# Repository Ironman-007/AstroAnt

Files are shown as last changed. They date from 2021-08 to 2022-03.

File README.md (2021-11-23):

# AstroAnt
Phase II of Rovables

The AstroAnt is the second generation of the Rovable project. The AstroAant also use magnetic wheels to attach to magnetic surface.

The AstroAnt is a modular design, and can carry different sensors to finish different kinds of diognostic missions, such as finding abnormal heating source, check CO2 leakage, detect metal flaw, and streaming video from remote.

Files descriptions:

- The 3D model of the robot is in the [Small_magnets_R821_with_gearbox](3dmodel/Small_magnets_R821_with_gearbox).

- The firmware of the robot is in [AstroAnt](Software/AstroAnt).

- The PC program (UI) is the [gui.py](Software/GUI_python/gui.py). Open with command line: ```python3 gui.py```

- The PCB design is in the [PCB](PCB). The [mainboard_v1](PCB/Mainboard/mainboard_v1/) is the design of the main control board, developed with KiCAD. The others are sensor modules design.

- The software of the central station for collecting data and distributing command is in [central_station](Software/Central_station/central_station/).

- The software of the central station for Camera in [cam_central](Software/Central_station/cam_central/).

- The Box design for the Zero-G flight test is in [Ant_Test_Box_DEC](3dmodel/Ant_Box_DEC/).

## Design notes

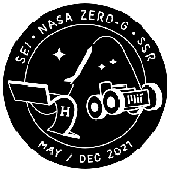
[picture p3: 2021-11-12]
PCB/Control_pad/patch-design-options3[3797].png

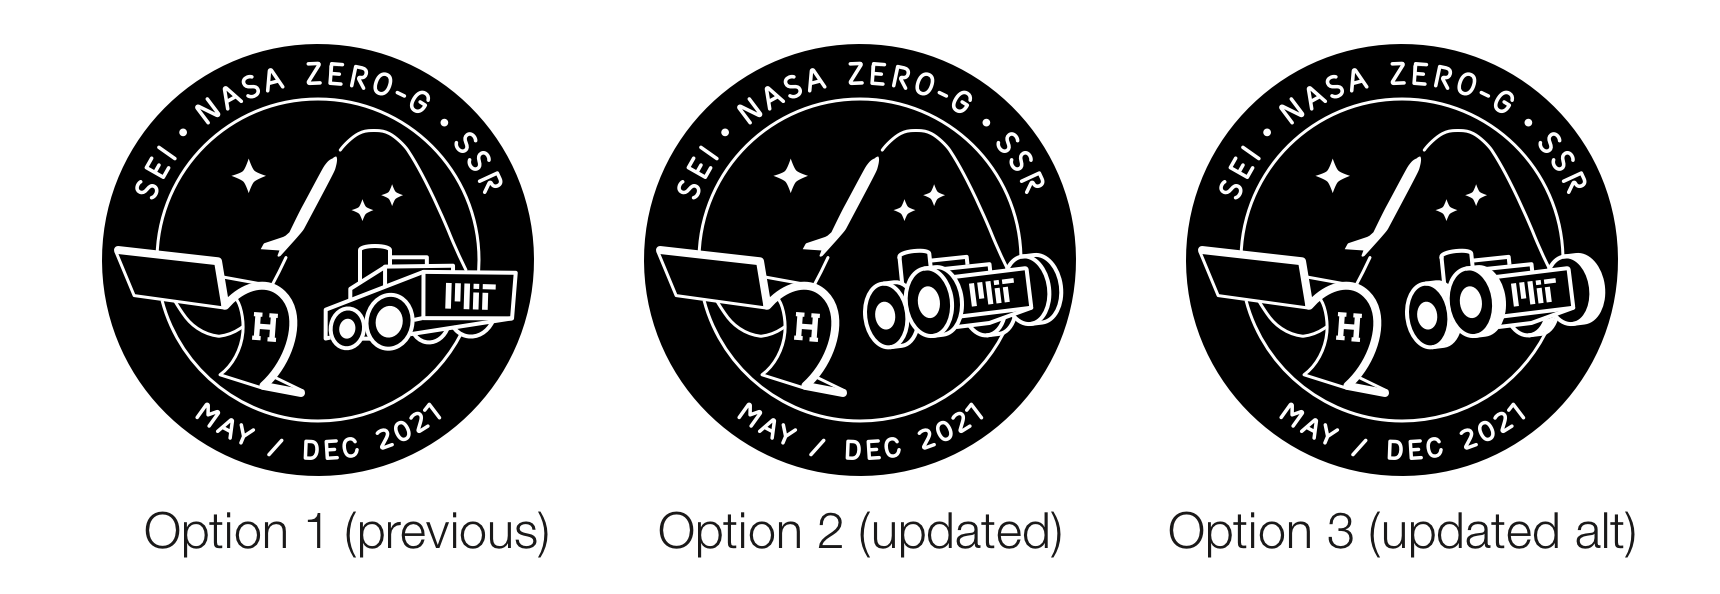
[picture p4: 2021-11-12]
PCB/Control_pad/patch-design-options3[3797] - Copy.png

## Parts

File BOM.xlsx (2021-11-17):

220mAh LiPo Battery | https://www.amazon.com/220mAh-Battery-Charger-Eachine-Quadcopter/dp/B07J3XJRF8
2x5x2.5mm ball bearing | https://www.amazon.com/2x5x2-5mm-MR52-ZZ-Precision-Bearings-Chrome/dp/B00TVPSCVO
Magnets | https://www.kjmagnetics.com/proddetail.asp?prod=RA22CS-N-N52
Ball bearing | https://www.amazon.com/uxcell-MR84-2RS-Bearing-4x8x3mm-Bearings/dp/B07TRQ19Y5
Name | Link | Qty | Vender
6mm pogo ping | https://www.amazon.com/Mxfans-Gold-plated-Copper-Needles-Connector/dp/B07FQF2BRC | 1 | amazon
9mm pogo ping | https://www.amazon.com/Mxfans-Gold-Plated-Copper-Needles-Thimble/dp/B07FQ52W88 | 1
SCD41 | https://www.digikey.com/en/products/detail/sensirion-ag/SCD41-D-R2/13684005 | 5 | digikey
SCD40 | https://www.digikey.com/en/products/detail/sensirion-ag/SCD40-D-R2/13684003 | 5
TPIS 1S 1385 / 5029 | https://www.digikey.com/en/products/detail/excelitas-technologies/TPIS-1S-1385-5029/9760638 | 10
RJD3555HPPV30M | https://www.digikey.com/en/products/detail/illinois-capacitor/RJD3555HPPV30M/6159145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 | 10
RFM97CW | https://www.sparkfun.com/products/18084 | 10 | Sparkfun
RFM95CW | https://www.sparkfun.com/products/18085 | 10
Aluminum frame | https://www.mcmaster.com/47065T101-47065T121/ | 10 | MacMaster Carr
Aluminum frame | https://www.mcmaster.com/47065T101-47065T209/ | 5
Handles | https://www.mcmaster.com/5190A3/ | 4
Screws | https://www.mcmaster.com/90991A122/ | 1
Screws | https://www.mcmaster.com/92832A334/ | 2
Screws | https://www.mcmaster.com/90991A123/ | 1
T-Slotted Framing | https://www.mcmaster.com/3136N153/ | 3
Flament (PETG) | https://www.matterhackers.com/store/l/pro-series-petg/sk/M89FGW3P | 2 | Matter hacker
Solder | https://www.amazon.com/dp/B0759P8GBZ | 1
Name | Link | Qty | Vender
nRF52840 module | https://www.amazon.com/Raytac-MDBT50Q-U1MV2-Bluetooth-Connector-Pre-Certified/dp/B0851WK785 | 1 | amazon
LoRa antenna | https://www.digikey.com/en/products/detail/linx-technologies-inc/ANT-916-USP/3830737 | 40 | digikey
RJD3555HPPV30M | https://www.digikey.com/en/products/detail/illinois-capacitor/RJD3555HPPV30M/6159145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 | 5
heat insert | https://www.amazon.com/Keadic-M3x6mmx5mm-Threaded-Embedment-Printing/dp/B08ZS6F5QW | 3 | amazon
heat insert | https://www.amazon.com/Keadic-M3x6mmx5mm-Threaded-Embedment-Printing/dp/B08ZRY23NH | 2
heat insert | https://www.amazon.com/Keadic-M3x6mmx5mm-Threaded-Embedment-Printing/dp/B08ZS4L8G7 | 2
Sensor | https://www.adafruit.com/product/3660 | 5 | adafruit
Weller solder tips | https://www.amazon.com/ShineNow-Quality-Replacement-WELLER-WE1010NA/dp/B071KYGZT8 | 1

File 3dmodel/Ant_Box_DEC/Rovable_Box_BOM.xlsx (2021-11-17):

ITEM NO. | PART NUMBER | Link | QTY. | unit price
1 | 47065T209_ALUMINUM T-SLOTTED FRAMING EXTRUSION | https://www.mcmaster.com/47065T101-47065T209/ | 20 | 7.79 | 155.8
2 | 47065T267_ALUMINUM T-SLOTTED FRAMING EXTRUSION | https://www.mcmaster.com/47065T267/ | 16 | 7.62 | 121.92
3 | 47065T278_ALUMINUM T-SLOTTED FRAMING EXTRUSION | https://www.mcmaster.com/47065T278/ | 6 | 7.95 | 47.7
4 | 8982K5_4ft | https://www.mcmaster.com/8982K54-8982K541/ | 1 | 2.73 | 2.73
5 | 8982K5_2ft | https://www.mcmaster.com/8982K54-8982K546/ | 2 | 1.65 | 3.3
6 | 47065T239 | https://www.mcmaster.com/47065T239/ | 8 | 5.25 | 42
8 | 47065T236 | https://www.mcmaster.com/47065T236/ | 17 | 5.21 | 88.57
9 | 47065T736_T-SLOTTED FRAMING | https://www.mcmaster.com/47065T736/ | 8 | 9.99 | 79.92
10 | 92198A628 | https://www.mcmaster.com/92198A628/ | 1 | 3.47 | 3.47
11 | 1/4_20_nut | https://www.mcmaster.com/94600A500/ | 1 | 13.38 | 13.38
12 | Framing fastener | https://www.mcmaster.com/3136N279/ | 15 | 4.73 | 70.95
13 | 1/4_20_5/8_screw_flat | https://www.mcmaster.com/97654A353/ | 8 | 6.35 | 50.8
14 | 1/4_20_1/2_screw_flat | https://www.mcmaster.com/97654A262/ | 5 | 4.8 | 24
15 | 1/4_20_1/2_screw | https://www.mcmaster.com/92949A537/ | 2 | 5.57 | 11.14
 |  |  |  | Total | 715.68
Note: Please use this address for this order: Fangzheng Liu 75 Amherst St E14-548 (responsive environments group) Cambridge, MA 02142-1322

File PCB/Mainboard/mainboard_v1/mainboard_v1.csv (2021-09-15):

Id | Designator | Package | Quantity | Designation | Supplier and ref
1 | S1 | Switch_Tactile_SMD_B3U-1000P | 1 | B3U-1000P
2 | J20,J19,J18,J17,J16,J15,J14,J13,J12,J11,J10,J9 | 1.27mm_pin_hole | 12 | 1_pin_sig
3 | J6 | 2002132100014C1LF | 1 | 20021321-00014C1LF
4 | IC2,IC1 | SOT95P280X100-6N | 2 | MP6513GJ-Z
5 | H1,H3,H2 | mounthole_1.8mm | 3 | M2
6 | R11,R10 | R_0603_1608Metric_Pad0.98x0.95mm_HandSolder | 2 | 10k
7 | J4 | PinHeader_2x01_P1.27mm_Vertical | 1 | 22-23-2021
8 | C13,C9 | CAPPM2014X170N | 2 | TAJP106K010RNJ
9 | U7,U4 | SOT-23-5_HandSoldering | 2 | AP2112K-3.3
10 | C18,C12,C8,C4,C1,C11 | C_0603_1608Metric_Pad1.08x0.95mm_HandSolder | 6 | 0.1uF
11 | C17,C16,C15,C14,C2,C10 | C_0603_1608Metric_Pad1.08x0.95mm_HandSolder | 6 | 10uF
12 | XTAL1 | ECS32712512TR | 1 | 32.768KHz
13 | J8,J3 | 17345926 | 2 | 1734592-6
14 | J7,J5 | HARWIN_M50-3100545 | 2 | 20021321-00010C4LF
15 | U5 | IC_MPU6050 | 1 | MPU6050
16 | C7 | C_0603_1608Metric_Pad1.08x0.95mm_HandSolder | 1 | 2200pF
17 | C3 | C_0603_1608Metric_Pad1.08x0.95mm_HandSolder | 1 | 10000pF
18 | U3 | SOT-23-5_HandSoldering | 1 | MCP73831T-2ACI_OT
19 | U1 | XCVR_MDBT50Q-1MV2 | 1 | MDBT50Q-1MV2
20 | C5,C6 | C_0603_1608Metric_Pad1.08x0.95mm_HandSolder | 2 | 22PF
21 | D1,D2,D3,D4 | LED_0603_1608Metric_Pad1.05x0.95mm_HandSolder | 4 | LED
22 | J1 | PinHeader_1x02_P1.27mm_Vertical | 1 | 22-23-2021
23 | J2 | USB_Micro-B_Amphenol_10104110_Horizontal | 1 | USB_B_Micro
24 | L1 | L_0603_1608Metric_Pad1.05x0.95mm_HandSolder | 1 | 10uH
25 | R1,R2 | R_0603_1608Metric_Pad0.98x0.95mm_HandSolder | 2 | 100k
26 | R3,R4,R5,R7 | R_0603_1608Metric_Pad0.98x0.95mm_HandSolder | 4 | 1k
27 | R6 | R_0603_1608Metric_Pad0.98x0.95mm_HandSolder | 1 | 4.99k
28 | R8,R9 | R_0603_1608Metric_Pad0.98x0.95mm_HandSolder | 2 | 27
29 | SW1 | SW_SPDT_PCM12 | 1 | SW_SPDT

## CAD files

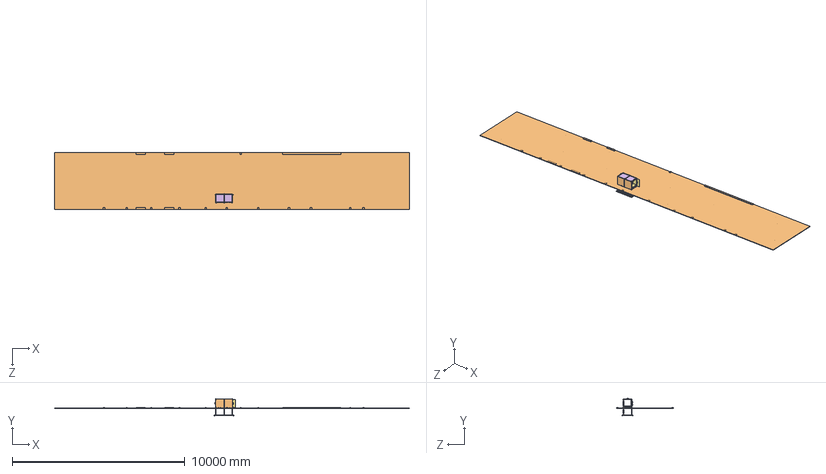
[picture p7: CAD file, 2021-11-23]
3dmodel/Ant_Box_DEC/Rovable_box.SLDASM
20574.0 x 992.2 x 3302.0 mm
47065T209_ALUMINUM T-SLOTTED FRAMING EXTRUSION x 23
47065T267_ALUMINUM T-SLOTTED FRAMING EXTRUSION x 24
47065T278_ALUMINUM T-SLOTTED FRAMING EXTRUSION x 6
8982K54 x 2
47065T239_ALUMINUM T-SLOTTED FRAMING EXTRUSION x 8
92949A562_18-8 SS BUTTON HEAD HEX DRIVE SCREW x 107
fabric_flat
metal_flat
aluminum_flat
side2 x 2
47065T236_ALUMINUM T-SLOTTED FRAMING EXTRUSION
8982K514_beam_1
base
ceiling x 2
door x 2
47065T736_T-SLOTTED FRAMING x 14
5193A200_RECTANGULAR LOAD-RATED NYLON PULL HANDLE x 6
91845A105_TYPE 18-8 STAINLESS STEEL HEX NUT x 3
97654A262_18-8 SS FLANGED BUTTON HEAD SCREW x 2
3136N279_T-SLOTTED FRAMING x 2
97654A353_18-8 SS FLANGED BUTTON HEAD SCREW
platform_big x 2
3136N153_T-Slotted Framing x 2
47065T209_T-Slotted Framing x 4
short_47065T209_T-Slotted Framing x 2

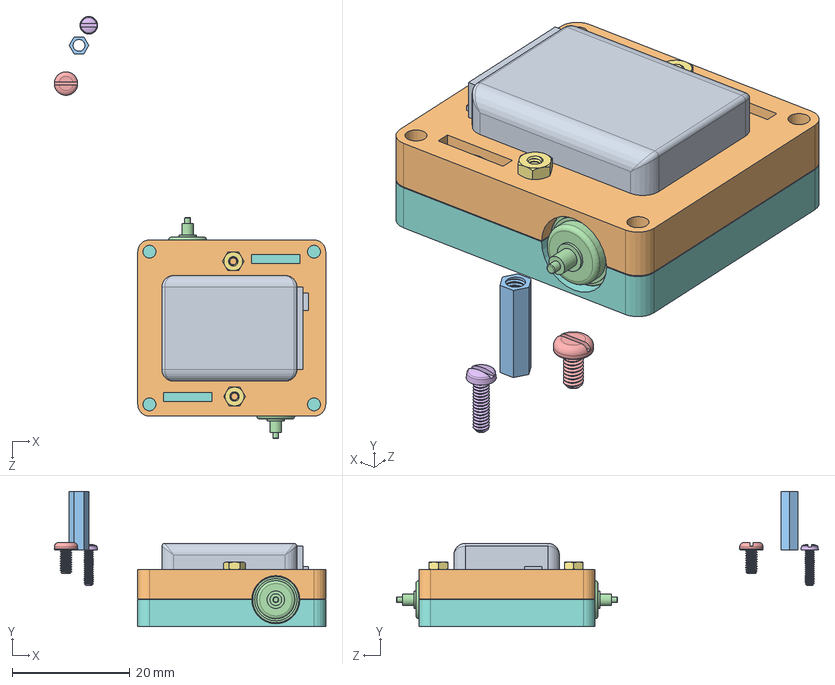
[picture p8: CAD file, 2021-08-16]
3dmodel/AstroAnt.SLDASM
46.2 x 23.1 x 71.8 mm
PA2-50 x 2
91828A006_18-8 Stainless Steel Hex Nut x 2
moto_holder

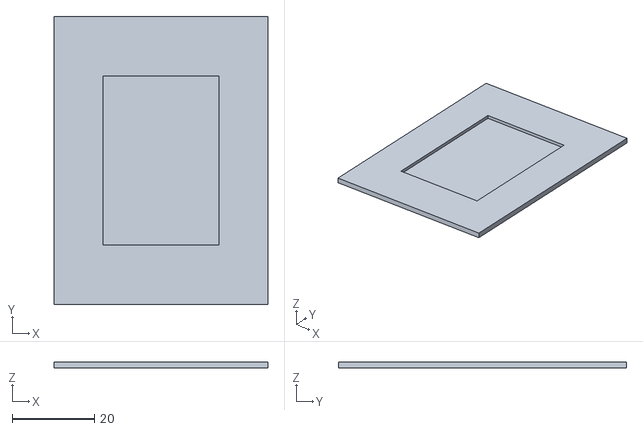
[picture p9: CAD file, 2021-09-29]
3dmodel/Printing/main_board_frame.STL
52.0 x 70.0 x 1.55

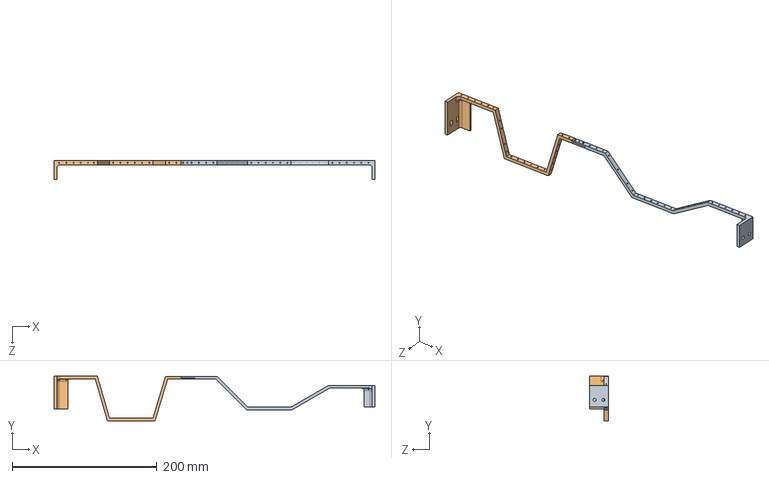
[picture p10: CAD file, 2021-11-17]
3dmodel/Ant_Box_DEC/fabric_ob2.SLDASM
443.6 x 61.6 x 26.0 mm
fabric_frame3
fab_frame4

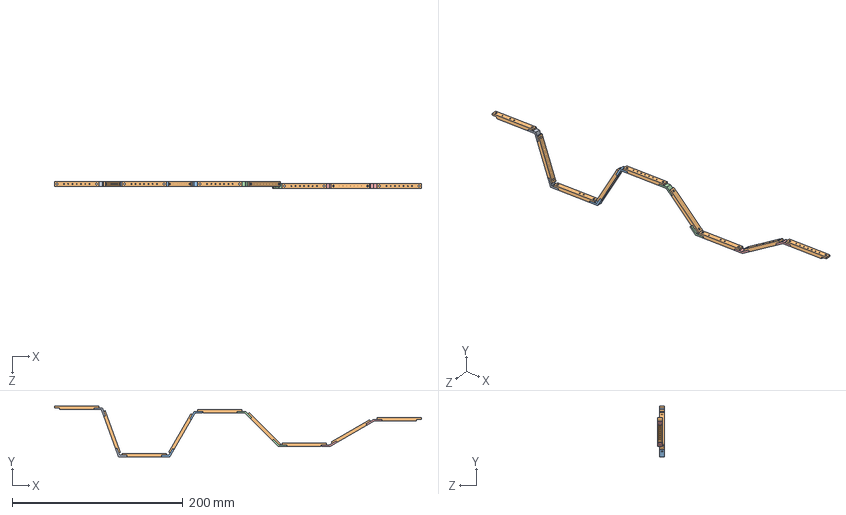
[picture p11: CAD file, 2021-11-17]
3dmodel/Ant_Box_DEC/fabric_ob.SLDASM
429.4 x 59.3 x 8.44 mm
fabric_ob_110 x 2
fabric_ob_beam x 9
fabric_ob_120 x 2
fabric_ob_135 x 2
fabric_ob_150 x 2

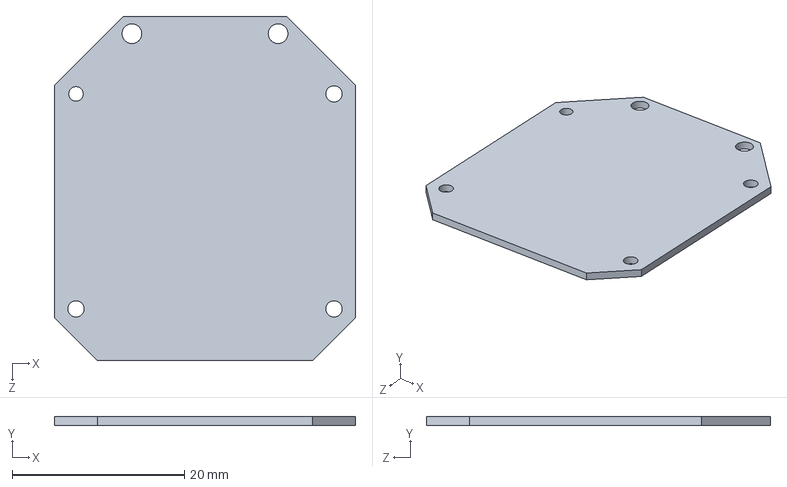
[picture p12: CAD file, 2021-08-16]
3dmodel/Small_magnets_R821_with_gearbox_IR_camera/main_board.sldprt
35.0 x 1.00 x 40.0 mm

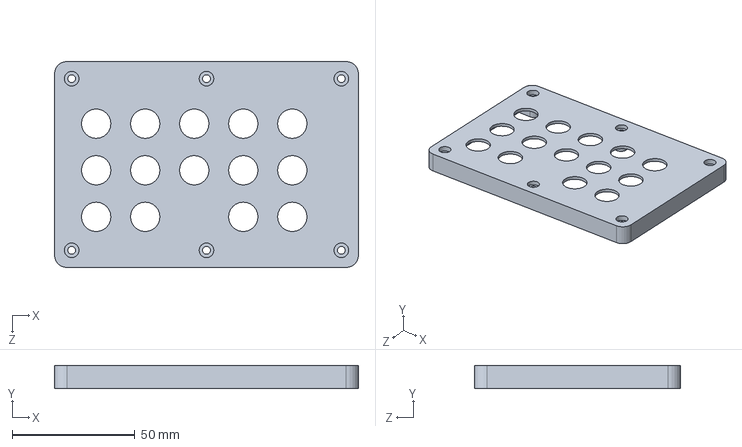
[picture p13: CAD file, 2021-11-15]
3dmodel/central_station/pad_lid.sldprt
124.0 x 9.50 x 84.0 mm

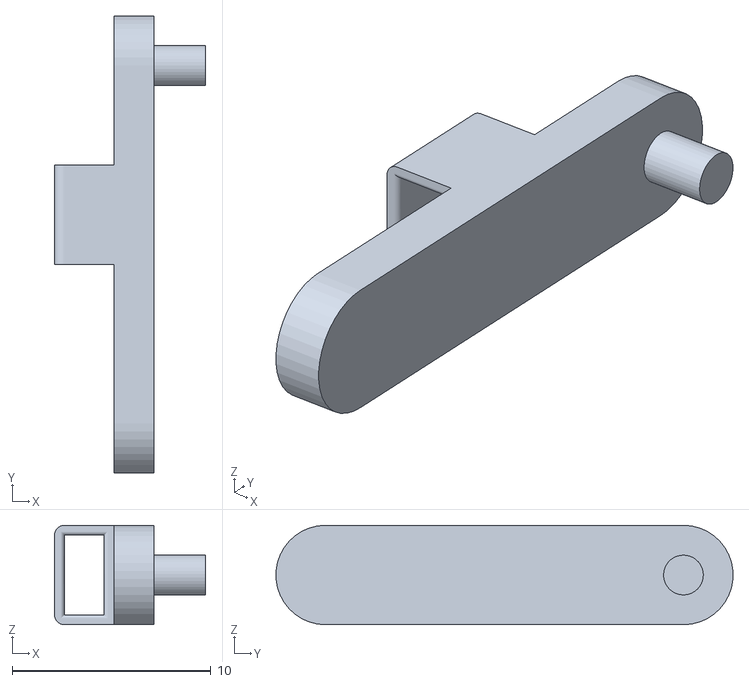
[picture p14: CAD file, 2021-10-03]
3dmodel/Printing/Knock/knock_knob.STL
7.60 x 23.0 x 5.00

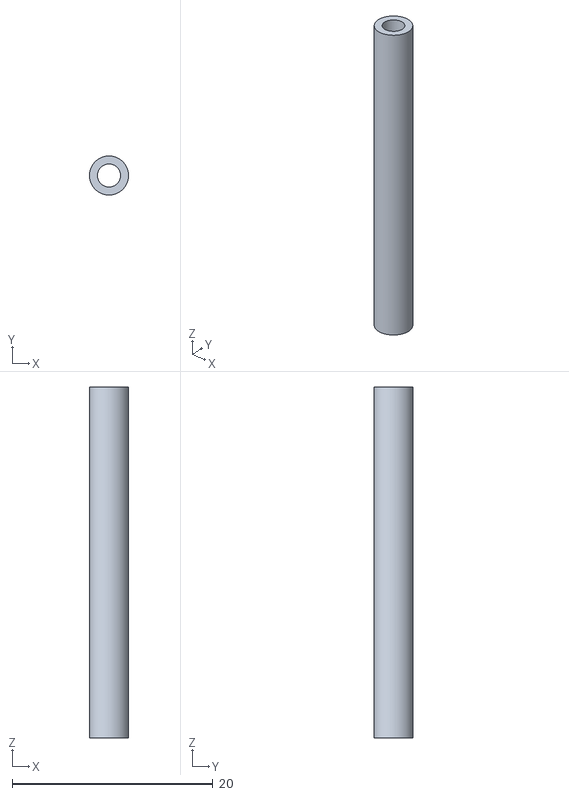
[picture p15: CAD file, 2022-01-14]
3dmodel/Printing/knocking_stick.stl
3.90 x 3.90 x 35.0

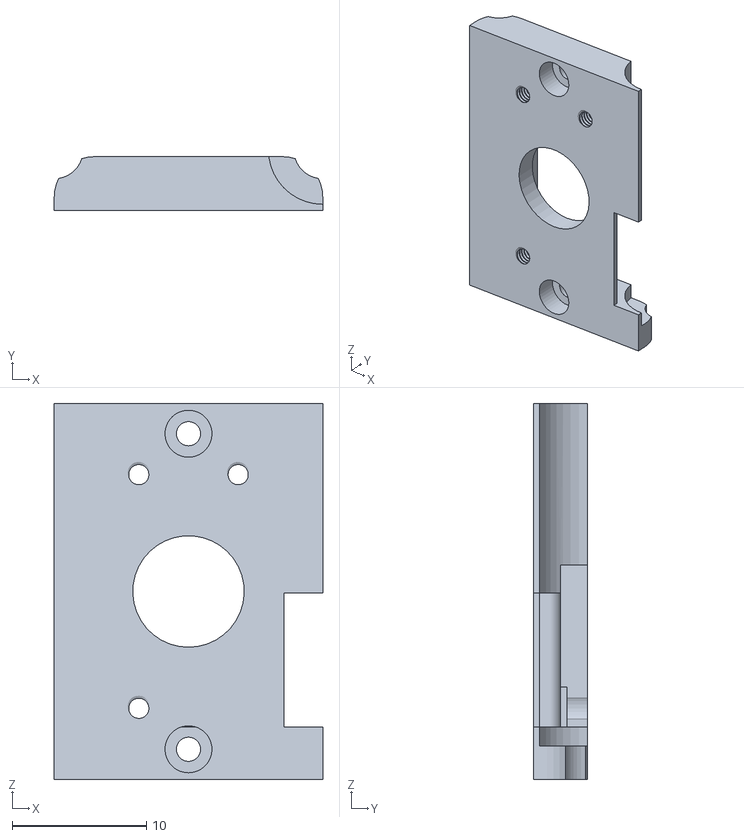
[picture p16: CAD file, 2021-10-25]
3dmodel/Small_magnets_R821/printing/motor_holder.STL
20.0 x 4.00 x 28.0

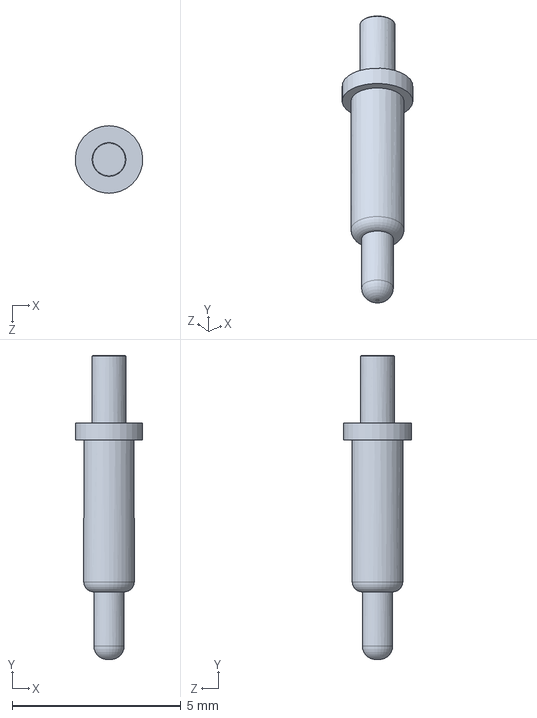
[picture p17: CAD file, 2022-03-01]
3dmodel/Small_magnets_R821_with_gearbox_IR_camera/9mm_pogo_pin.sldprt
2.00 x 9.00 x 2.00 mm

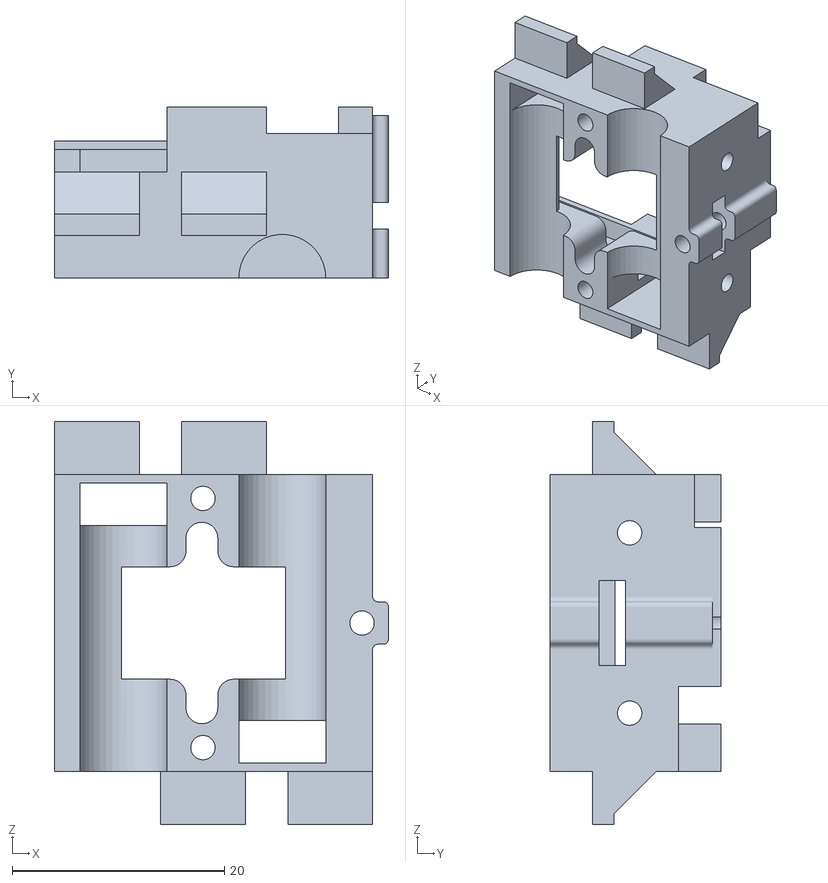
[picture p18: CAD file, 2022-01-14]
3dmodel/Small_magnets_R821_with_gearbox_IR_camera/printing/robobody_big_bat_impedance.STL
31.5 x 16.1 x 38.0

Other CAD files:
3dmodel/Small_magnets_R821_with_gearbox_IR_camera/main_board_frame.SLDPRT
3dmodel/Small_magnets_R821_with_gearbox_IR_camera/Bot_380f.step.SLDASM
3dmodel/Small_magnets_R821_with_gearbox_IR_camera/Top_380f.step.SLDASM
3dmodel/Small_magnets_R821_with_gearbox_IR_camera/U1_ASSEMBLY_613A7E1B.step.SLDASM
3dmodel/Small_magnets_R821_with_gearbox_IR_camera/J1_ASSEMBLY_613A7DC7.step.SLDASM
3dmodel/Life_time_test/base_2.sldprt
3dmodel/Ant_Box_DEC/3136N153_T-Slotted Framing.SLDPRT
3dmodel/Ant_Box_DEC/3136N279_T-SLOTTED FRAMING.SLDPRT
3dmodel/Ant_Box_DEC/47065T209_ALUMINUM T-SLOTTED FRAMING EXTRUSION.SLDPRT
3dmodel/Ant_Box_DEC/47065T209_ALUMINUM_long.SLDPRT
3dmodel/Ant_Box_DEC/47065T209_T-Slotted Framing.SLDPRT
3dmodel/Ant_Box_DEC/47065T209_short.SLDPRT
3dmodel/Ant_Box_DEC/47065T236_ALUMINUM T-SLOTTED FRAMING EXTRUSION.SLDPRT
3dmodel/Ant_Box_DEC/47065T239_ALUMINUM T-SLOTTED FRAMING EXTRUSION.SLDPRT
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

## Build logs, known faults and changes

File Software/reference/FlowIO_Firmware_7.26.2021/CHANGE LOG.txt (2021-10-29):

This firmware uses the updated library featuring the optimizePower() function. 

<<<<<<< HEAD
The _holdPWM value is set to a fixed 150, based on the various measurements I did on the valves and battery. I can lowere this value even further when the battery is fresh, to save even more power. But then I gradually needs to increase it back to 150 as the battery voltage starts dropping - in order to maintain a steady average voltage at the valves.

There are also some commends added to the batteryService.ino file about what needs to be done there in the futre. Namely to include the battery features directly into the API, so that the optimizePower() function takes care of even adjusting the _holdPWM value. 

The next immediate step is to add a battery fuction in the API itself, and thus simplify the battery service a little bit. After that is done, I can then implement the low battery LED indicator properly, as well as implement the dynamic _holdPWM value.
=======
The _holdPWM value is set to a fixed 150, based on the various measurements I did on the valves and battery. I can lower this value even further when the battery is fresh, to save even more power. But then I gradually needs to increase it back to 150 as the battery voltage starts dropping - in order to maintain a steady average voltage at the valves.

There are also some commends added to the batteryService.ino file about what needs to be done there in the future. Namely to include the battery features directly into the API, so that the optimizePower() function takes care of even adjusting the _holdPWM value. 

The next immediate step is to add a battery function in the API itself, and thus simplify the battery service a little bit. After that is done, I can then implement the low battery LED indicator properly, as well as implement the dynamic _holdPWM value.
>>>>>>> 2d34b99e5713db9c35350437761a65dbaa9e3cf3

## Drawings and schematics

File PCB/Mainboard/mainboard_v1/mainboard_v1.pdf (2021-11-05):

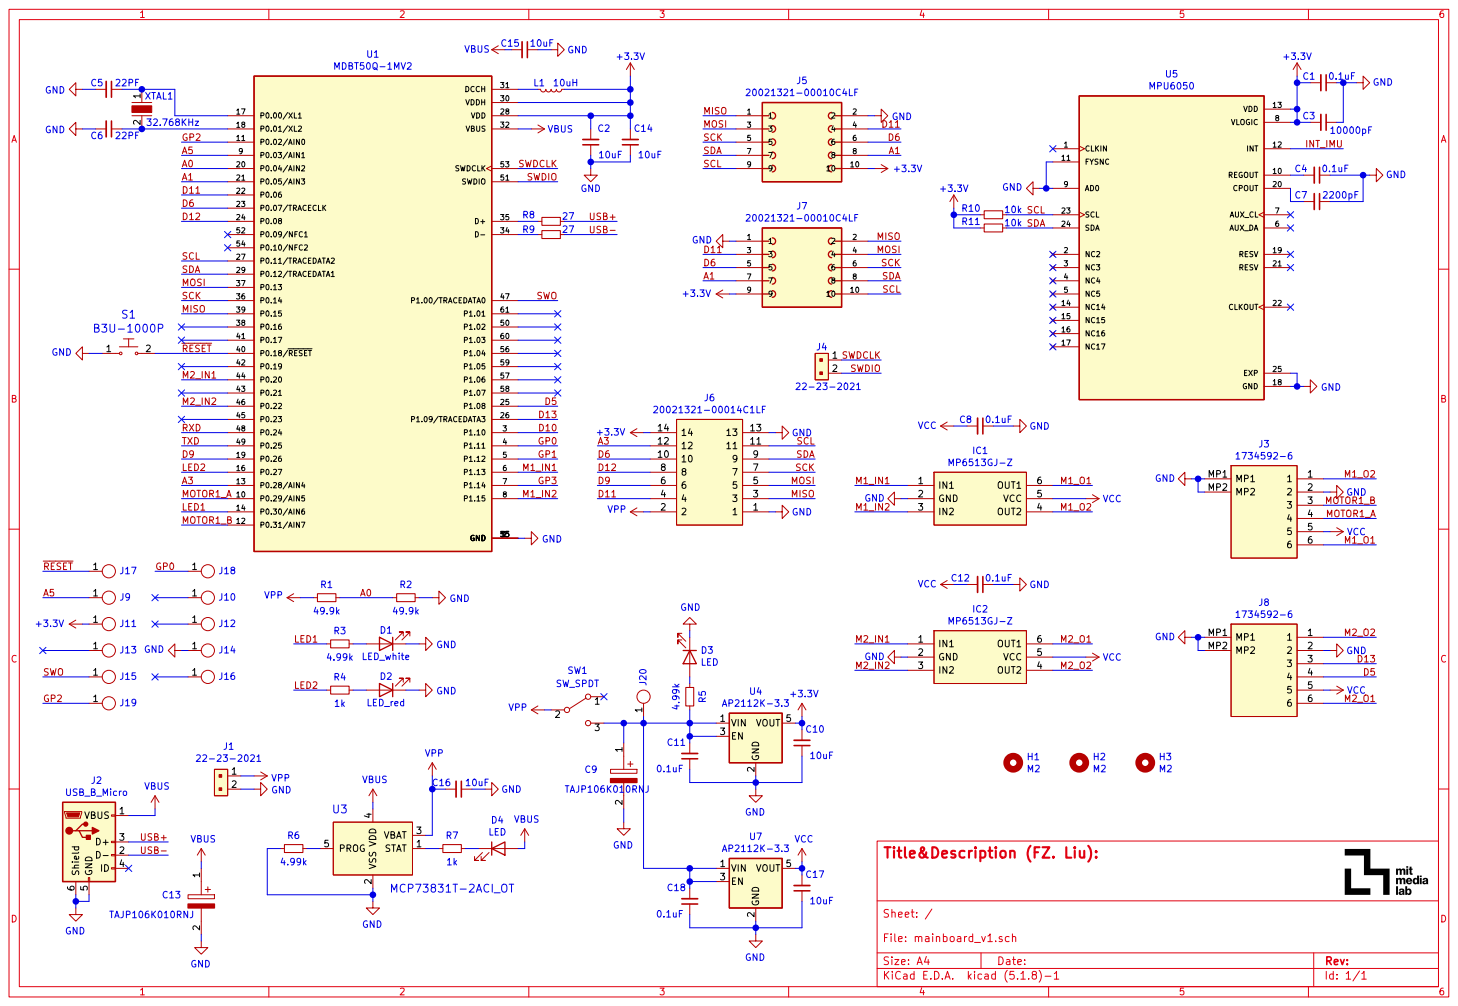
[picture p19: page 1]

Id: 1/1 Title&Description (FZ. Liu):

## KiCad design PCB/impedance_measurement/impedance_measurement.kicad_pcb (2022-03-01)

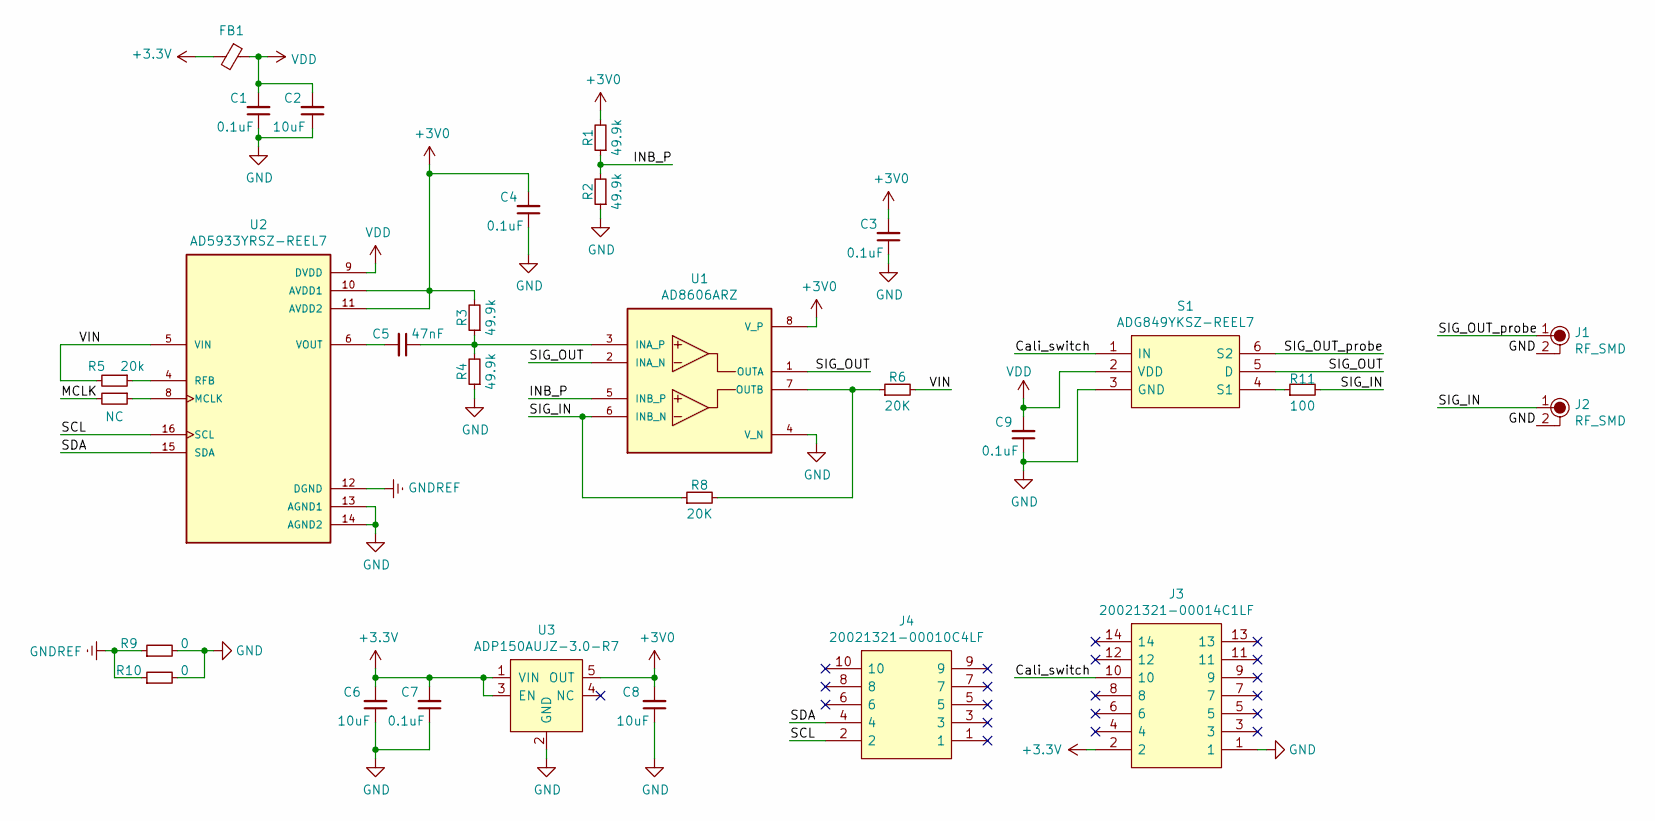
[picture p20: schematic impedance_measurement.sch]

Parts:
C1, C3, C4, C7, C9: 0.1uF; C_0603_1608Metric_Pad1.08x0.95mm_HandSolder
C2, C6, C8: 10uF; C_0603_1608Metric_Pad1.08x0.95mm_HandSolder
C5: 47nF; C_0402_1005Metric_Pad0.74x0.62mm_HandSolder
FB1: Ferrite_Bead_Small; C_0603_1608Metric_Pad1.08x0.95mm_HandSolder
J1, J2: RF_SMD
J3: 20021321-00014C1LF; PinHeader_2x07_P1.27mm_Vertical; Manufacturer_Part_Number 20021321-00014C1LF; Mouser Part Number 649-20213210014C1LF
J4: 20021321-00010C4LF; PinHeader_2x05_P1.27mm_Vertical; Manufacturer_Part_Number 20021321-00010C4LF; Mouser Part Number 649-202132100010C4LF
R1, R2, R3, R4: 49.9k; R_0402_1005Metric_Pad0.72x0.64mm_HandSolder
R5: 20k; R_0402_1005Metric_Pad0.72x0.64mm_HandSolder
R6: 20K; R_0402_1005Metric_Pad0.72x0.64mm_HandSolder
R7: NC; R_0402_1005Metric_Pad0.72x0.64mm_HandSolder
R8: 20K; R_0603_1608Metric_Pad0.98x0.95mm_HandSolder
R9, R10: 0; R_0402_1005Metric_Pad0.72x0.64mm_HandSolder
R11: 100; R_0805_2012Metric_Pad1.20x1.40mm_HandSolder
S1: ADG849YKSZ-REEL7; SOT65P210X110-6N; Manufacturer_Part_Number ADG849YKSZ-REEL7; Mouser Part Number 584-ADG849YKSZ-R7
U1: AD8606ARZ; SOIC127P600X175-8N; PARTREV Rev. O
U2: AD5933YRSZ-REEL7; SOP65P780X200-16N; PARTREV F
U3: ADP150AUJZ-3.0-R7; TSOT-23-5

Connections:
+3V0: C3.2, C4.2, C8.2, R1.2, R3.2, U1.8 (V_P), U2.10 (AVDD1), U2.11 (AVDD2), U3.5 (OUT)
+3V3: C6.2, C7.2, FB1.2, J3.2, U3.1 (VIN), U3.3 (EN)
/Cali_switch: J3.10, S1.1 (IN)
/INB_P: R1.1, R2.2, U1.5 (INB_P)
/SCL: J4.2, U2.16 (SCL)
/SDA: J4.4, U2.15 (SDA)
/SIG_IN: J2.1, R8.1, R11.2, U1.6 (INB_N)
/SIG_OUT: S1.5 (D), U1.1 (OUTA), U1.2 (INA_N)
/SIG_OUT_probe: J1.1, S1.6 (S2)
/VIN: R5.2, R6.2, U2.5 (VIN)
GND: C1.1, C2.1, C3.1, C4.1, C6.1, C7.1, C8.1, C9.1, J1.2, J2.2, J3.1, R2.1, R4.1, R9.2, R10.2, S1.3 (GND), U1.4 (V_N), U2.13 (AGND1), U2.14 (AGND2), U3.2 (GND)
GNDREF: R9.1, R10.1, U2.12 (DGND)
unnamed: C5.1, R3.1, R4.2, U1.3 (INA_P)
unnamed: C5.2, U2.6 (VOUT)
unnamed: R5.1, U2.4 (RFB)
unnamed: R6.1, R8.2, U1.7 (OUTB)
unnamed: R7.1, U2.8 (MCLK)
unnamed: R11.1, S1.4 (S1)
VDD: C1.2, C2.2, C9.2, FB1.1, S1.2 (VDD), U2.9 (DVDD)

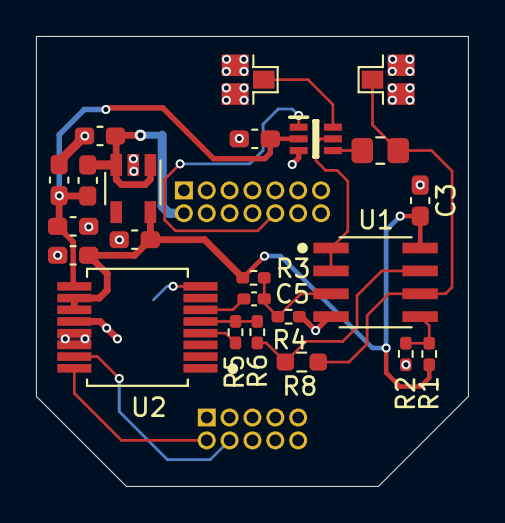
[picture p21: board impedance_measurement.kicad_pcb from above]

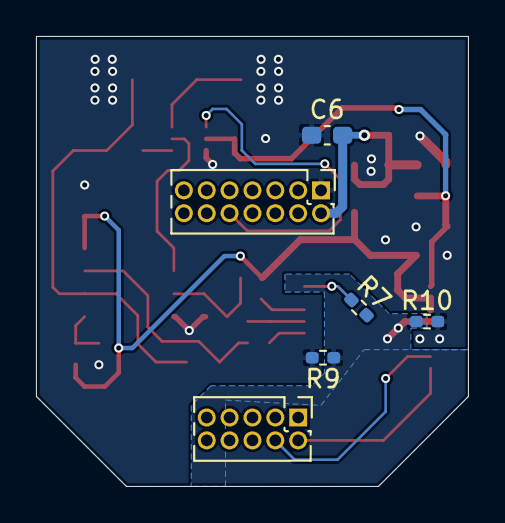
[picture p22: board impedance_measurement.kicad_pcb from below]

Board: 2 copper layers, 24.0 x 25.0 mm, 29 parts (6 on the bottom side), 19 nets.

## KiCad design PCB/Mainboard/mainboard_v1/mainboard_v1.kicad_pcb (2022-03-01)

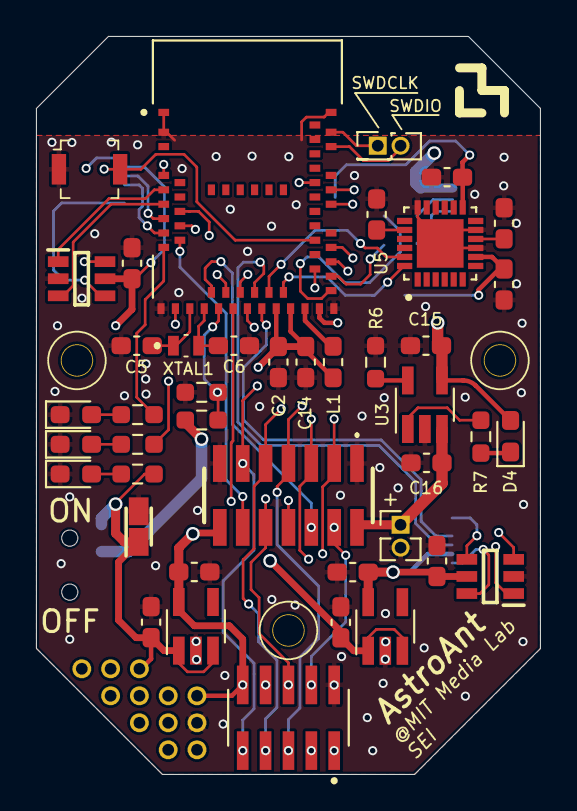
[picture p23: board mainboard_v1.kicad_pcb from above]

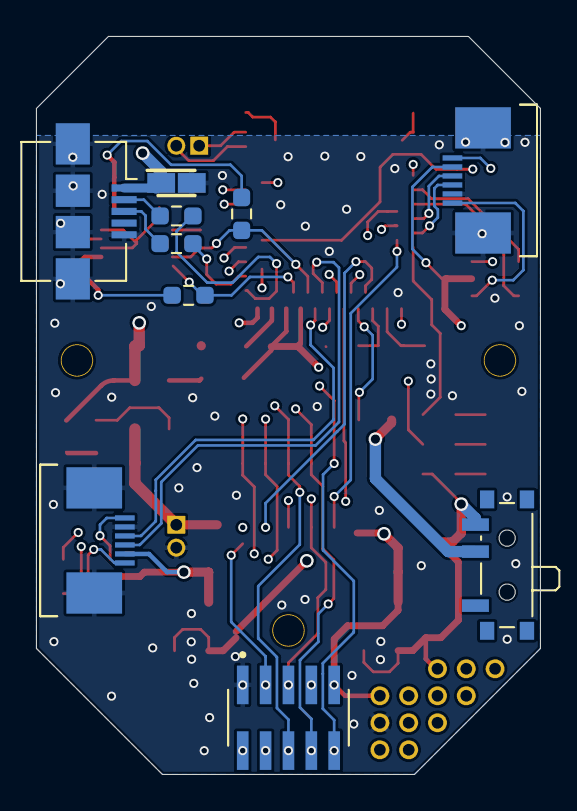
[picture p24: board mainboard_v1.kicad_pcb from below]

Board: 4 copper layers, 28.0 x 41.0 mm, 67 parts (10 on the bottom side), 54 nets.

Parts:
C1, C4, C8, C11, C12, C18: 0.1uF; C_0603_1608Metric_Pad1.08x0.95mm_HandSolder
C2, C10, C14, C15, C16, C17: 10uF; C_0603_1608Metric_Pad1.08x0.95mm_HandSolder
C3: 10000pF; C_0603_1608Metric_Pad1.08x0.95mm_HandSolder
C5, C6: 22PF; C_0603_1608Metric_Pad1.08x0.95mm_HandSolder
C7: 2200pF; C_0603_1608Metric_Pad1.08x0.95mm_HandSolder
C9, C13: TAJP106K010RNJ; CAPPM2014X170N
D1: LED_white; LED_0603_1608Metric_Pad1.05x0.95mm_HandSolder
D2: LED_red; LED_0603_1608Metric_Pad1.05x0.95mm_HandSolder
D3, D4: LED; LED_0603_1608Metric_Pad1.05x0.95mm_HandSolder
H1, H2, H3: M2; mounthole_1.8mm
IC1, IC2: MP6513GJ-Z; SOT95P280X100-6N
J1: 22-23-2021; PinHeader_1x02_P1.27mm_Vertical
J2: USB_B_Micro; USB_Micro-B_Amphenol_10104110_Horizontal
J3, J8: 1734592-6; 17345926
J4: 22-23-2021; PinHeader_2x01_P1.27mm_Vertical
J5, J7: 20021321-00010C4LF; HARWIN_M50-3100545
J6: 20021321-00014C1LF; 2002132100014C1LF
J9, J10, J11, J12, J13, J14, J15, J16, J17, J18, J19, J20: 1_pin_sig; 1.27mm_pin_hole
L1: 10uH; L_0603_1608Metric_Pad1.05x0.95mm_HandSolder
R1, R2: 49.9k; R_0603_1608Metric_Pad0.98x0.95mm_HandSolder
R3, R4, R5, R6: 4.99k; R_0603_1608Metric_Pad0.98x0.95mm_HandSolder
R7: 1k; R_0603_1608Metric_Pad0.98x0.95mm_HandSolder
R8, R9: 27; R_0603_1608Metric_Pad0.98x0.95mm_HandSolder
R10, R11: 10k; R_0603_1608Metric_Pad0.98x0.95mm_HandSolder
S1: B3U-1000P; Switch_Tactile_SMD_B3U-1000P
SW1: SW_SPDT; SW_SPDT_PCM12
U1: MDBT50Q-1MV2; XCVR_MDBT50Q-1MV2
U3: MCP73831T-2ACI_OT; SOT-23-5_HandSoldering
U4, U7: AP2112K-3.3; SOT-23-5_HandSoldering
U5: MPU6050; IC_MPU6050
XTAL1: 32.768KHz; ECS32712512TR

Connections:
+3V3: C1.2, C2.2, C3.2, C10.2, C14.2, J5.10, J6.14, J7.9, J11.1, L1.1, R10.2, R11.2, U1.28, U1.30, U4.5, U5.8, U5.13
/A0: R1.1, R2.2, U1.20
/A1: J5.8, J7.7, U1.21
/A3: J6.12, U1.13
/A5: J9.1, U1.9
/D5: J8.4, U1.25
/D6: J5.6, J6.10, J7.5, U1.23
/D9: J6.6, U1.19
/D11: J5.4, J6.4, J7.3, U1.22
/D12: J6.8, U1.24
/D13: J8.3, U1.26
/GP0: J18.1, U1.4
/GP2: J19.1, U1.11
/LED1: R3.2, U1.14
/LED2: R4.2, U1.16
/M1_IN1: IC1.1, U1.6
/M1_IN2: IC1.3, U1.8
/M1_O1: IC1.6, J3.6
/M1_O2: IC1.4, J3.1
/M2_IN1: IC2.1, U1.44
/M2_IN2: IC2.3, U1.46
/M2_O1: IC2.6, J8.6
/M2_O2: IC2.4, J8.1
/MISO: J5.1, J6.3, J7.2, U1.39
/MOSI: J5.3, J6.5, J7.4, U1.37
/MOTOR1_A: J3.4, U1.10
/MOTOR1_B: J3.3, U1.12
/SCK: J5.5, J6.7, J7.6, U1.36
/SCL: J5.9, J6.11, J7.10, R10.1, U1.27, U5.23
/SDA: J5.7, J6.9, J7.8, R11.1, U1.29, U5.24
/SWDCLK: J4.1, U1.53
/SWDIO: J4.2, U1.51
/SWO: J15.1, U1.47
/USB+: J2.3, R8.1
/USB-: J2.2, R9.1
/~RESET: J17.1, S1.2, U1.40
GND: C1.1, C2.1, C3.1, C4.1, C5.2, C6.2, C7.1, C8.1, C9.2, C10.1, C11.1, C12.1, C13.2, C14.1, C15.1, C16.1, C17.1, C18.1, D1.1, D2.1, D3.1, IC1.2, IC2.2, J1.2, J2.5, J2.6, J3.2, J3.MP1, J3.MP2, J5.2, J6.1, J6.13, J7.1, J8.2, J8.MP1, J8.MP2, J14.1, R2.1, R6.2, S1.1, U1.1, U1.2, U1.15, U1.33, U1.55, U3.2, U4.2, U5.9, U5.11, U5.18, U5.25, U7.2
unnamed: C4.2, U5.10
unnamed: C5.1, U1.17, XTAL1.1
unnamed: C6.1, U1.18, XTAL1.2
unnamed: C7.2, U5.20
unnamed: C9.1, C11.2, C18.2, J20.1, R5.1, SW1.3, U4.1, U4.3, U7.1, U7.3
unnamed: D1.2, R3.1
unnamed: D2.2, R4.1
unnamed: D3.2, R5.2
unnamed: D4.1, R7.1
unnamed: L1.2, U1.31
unnamed: R6.1, U3.5
unnamed: R7.2, U3.1
unnamed: R8.2, U1.35
unnamed: R9.2, U1.34
VBUS: C13.1, C15.2, D4.2, J2.1, U1.32, U3.4
VCC: C8.2, C12.2, C17.2, IC1.5, IC2.5, J3.5, J8.5, U7.5
VPP: C16.2, J1.1, J6.2, R1.2, SW1.2, U3.3

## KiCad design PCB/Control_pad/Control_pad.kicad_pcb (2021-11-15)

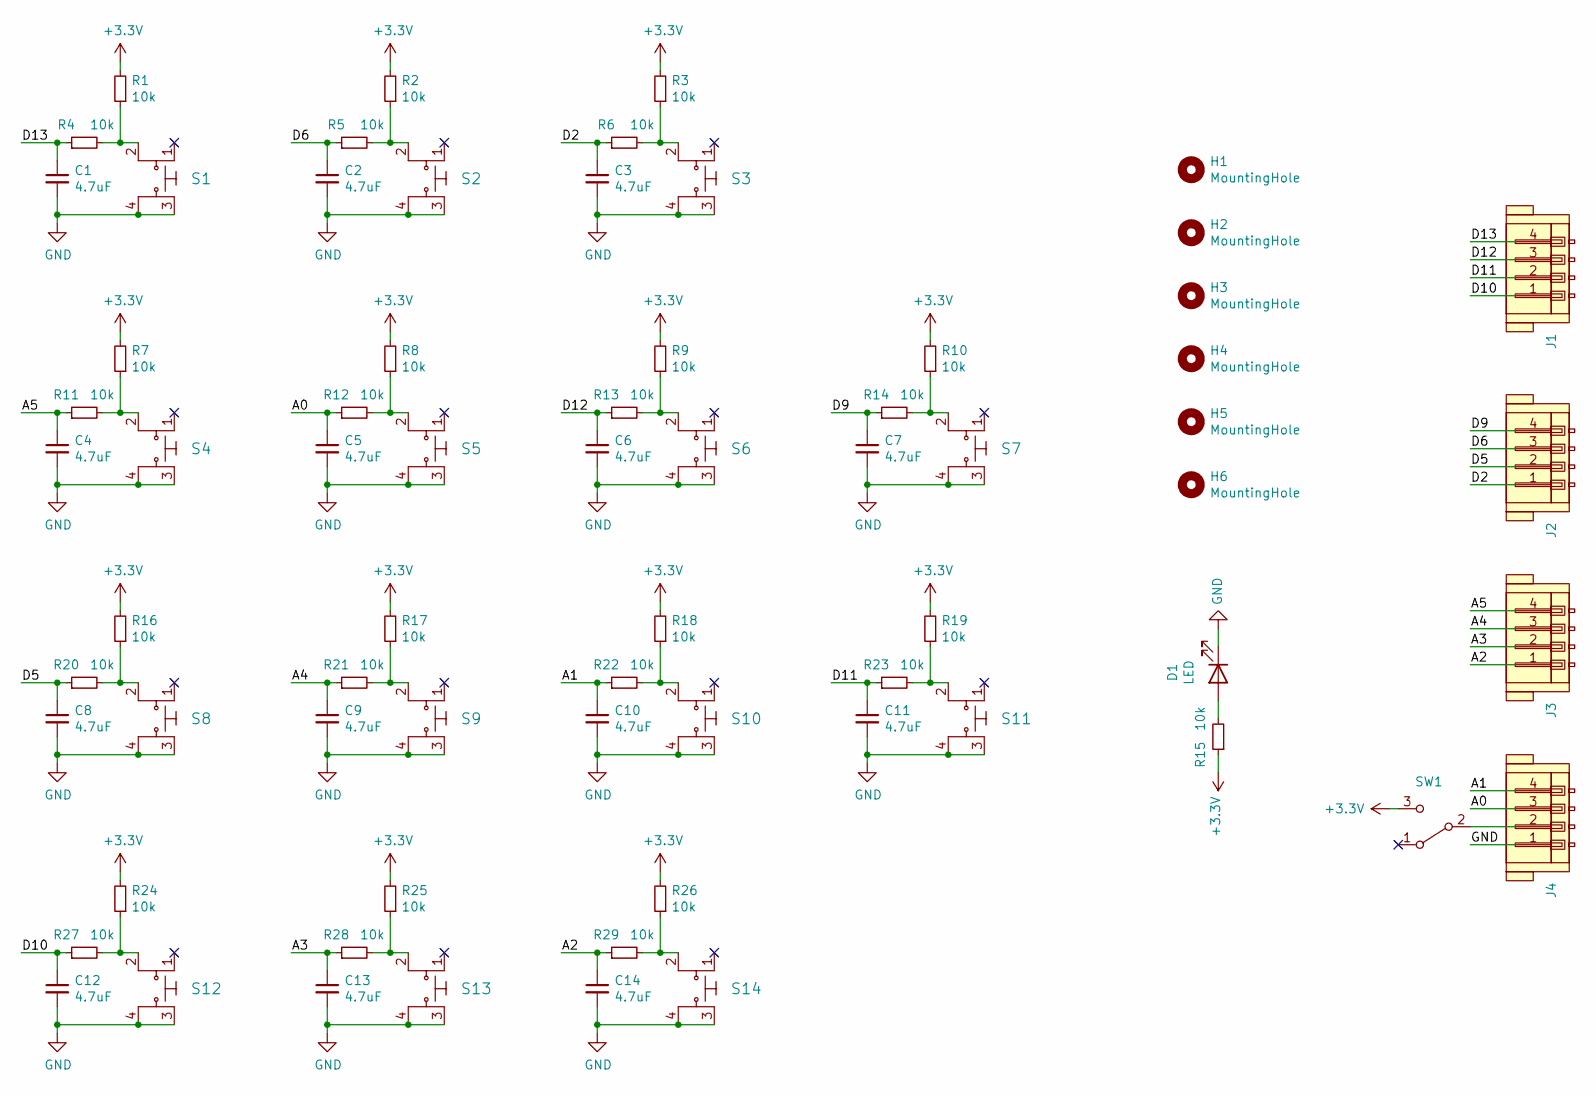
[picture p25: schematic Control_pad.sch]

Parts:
C1, C2, C3, C4, C5, C6, C7, C8, C9, C10, C11, C12, C13, C14: 4.7uF; C_0805_2012Metric_Pad1.18x1.45mm_HandSolder
D1: LED; LED_1206_3216Metric_Pad1.42x1.75mm_HandSolder
H1, H2, H3, H4, H5, H6: MountingHole; MountingHole_3.2mm_M3
J1, J2, J3, J4: JST_SH_4_pin_male; JST_XH_B4B-XH-A_1x04_P2.50mm_Vertical
R1, R2, R3, R4, R5, R6, R7, R8, R9, R10, R11, R12, R13, R14, R15, R16, R17, R18, R19, R20, R21, R22, R23, R24, R25, R26, R27, R28, R29: 10k; R_0805_2012Metric_Pad1.20x1.40mm_HandSolder
S1, S2, S3, S4, S5, S6, S7, S8, S9, S10, S11, S12, S13, S14: 1825910-6; TWTADE_12mmx12mm_tactile_switch; MPN 1825910-6; Digi-Key_PN 450-1650-ND
SW1: SW_SPDT; CYT1107

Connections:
+3V3: R1.2, R2.2, R3.2, R7.2, R8.2, R9.2, R10.2, R15.1, R16.2, R17.2, R18.2, R19.2, R24.2, R25.2, R26.2, SW1.3 (C)
/A0: C5.1, J4.3, R12.1
/A1: C10.1, J4.4, R22.1
/A2: C14.1, J3.1, R29.1
/A3: C13.1, J3.2, R28.1
/A4: C9.1, J3.3, R21.1
/A5: C4.1, J3.4, R11.1
/D2: C3.1, J2.1, R6.1
/D5: C8.1, J2.2, R20.1
/D6: C2.1, J2.3, R5.1
/D9: C7.1, J2.4, R14.1
/D10: C12.1, J1.1, R27.1
/D11: C11.1, J1.2, R23.1
/D12: C6.1, J1.3, R13.1
/D13: C1.1, J1.4, R4.1
GND: C1.2, C2.2, C3.2, C4.2, C5.2, C6.2, C7.2, C8.2, C9.2, C10.2, C11.2, C12.2, C13.2, C14.2, D1.1 (K), J4.1, S1.3, S1.4, S2.3, S2.4, S3.3, S3.4, S4.3, S4.4, S5.3, S5.4, S6.3, S6.4, S7.3, S7.4, S8.3, S8.4, S9.3, S9.4, S10.3, S10.4, S11.3, S11.4, S12.3, S12.4, S13.3, S13.4, S14.3, S14.4
unnamed: D1.2 (A), R15.2
unnamed: J4.2, SW1.2 (B)
unnamed: R1.1, R4.2, S1.2
unnamed: R2.1, R5.2, S2.2
unnamed: R3.1, R6.2, S3.2
unnamed: R10.1, R14.2, S7.2
unnamed: R7.1, R11.2, S4.2
unnamed: R8.1, R12.2, S5.2
unnamed: R9.1, R13.2, S6.2
unnamed: R16.1, R20.2, S8.2
unnamed: R17.1, R21.2, S9.2
unnamed: R18.1, R22.2, S10.2
unnamed: R19.1, R23.2, S11.2
unnamed: R24.1, R27.2, S12.2
unnamed: R25.1, R28.2, S13.2
unnamed: R26.1, R29.2, S14.2

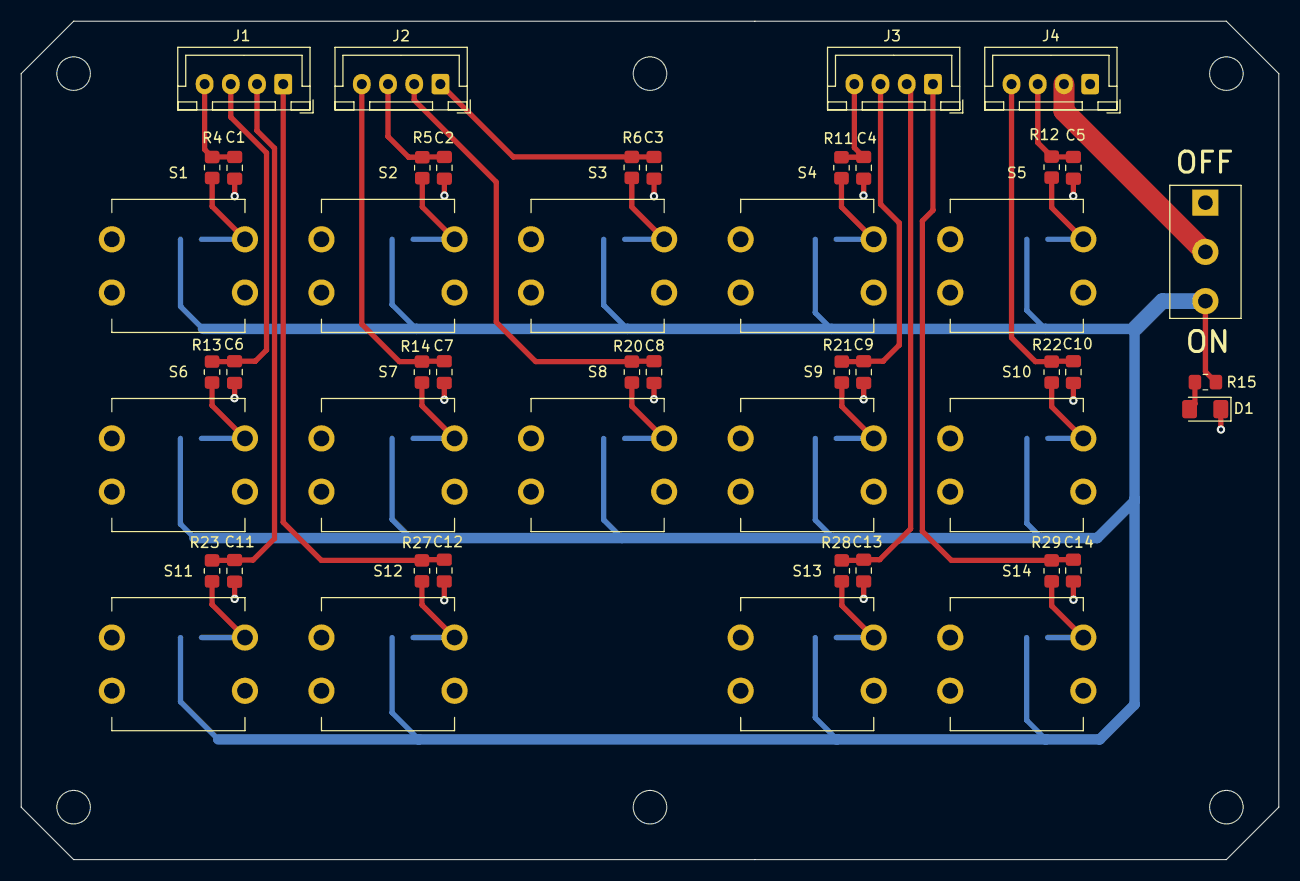
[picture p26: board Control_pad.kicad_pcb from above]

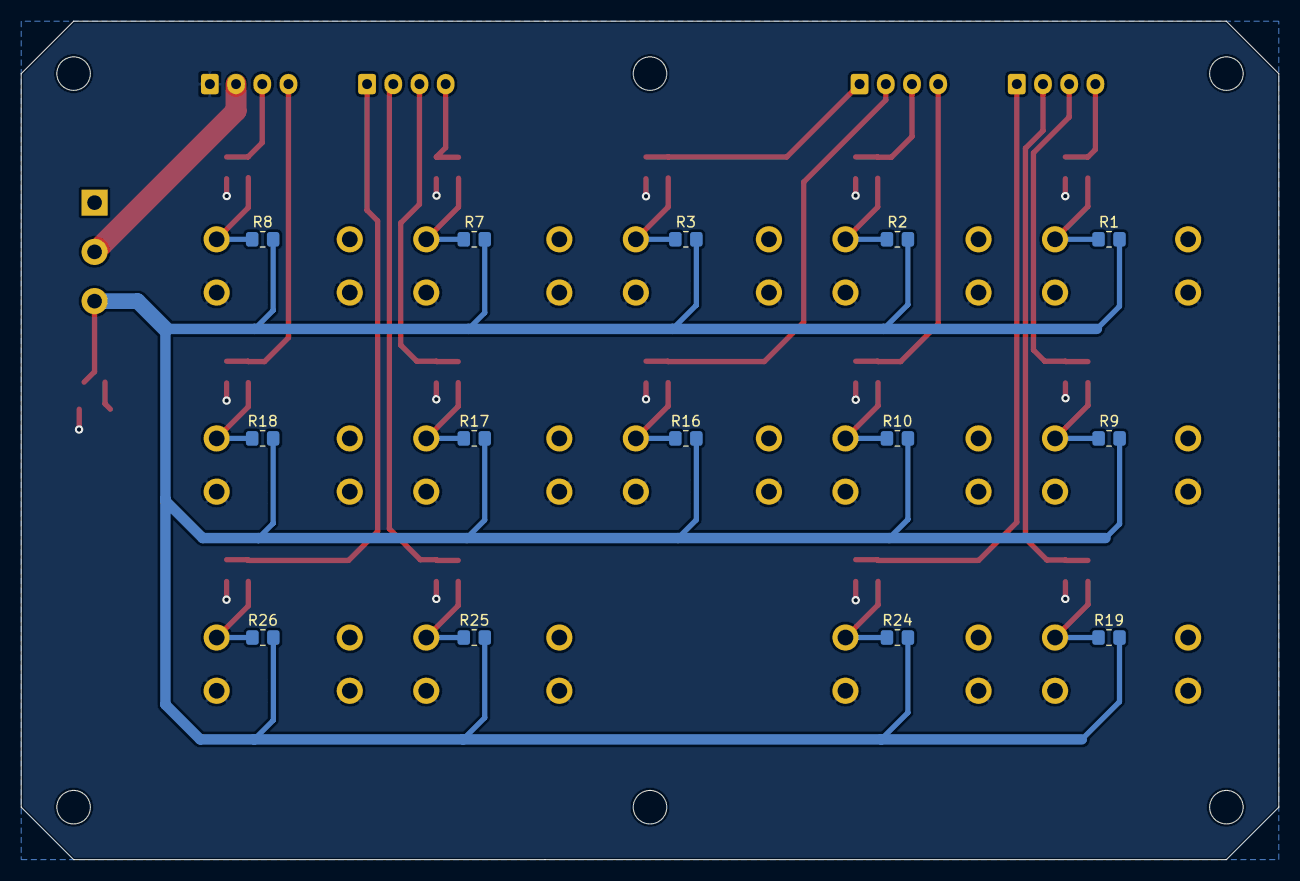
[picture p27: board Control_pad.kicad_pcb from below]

Board: 2 copper layers, 120.0 x 80.0 mm, 69 parts (14 on the bottom side), 32 nets.

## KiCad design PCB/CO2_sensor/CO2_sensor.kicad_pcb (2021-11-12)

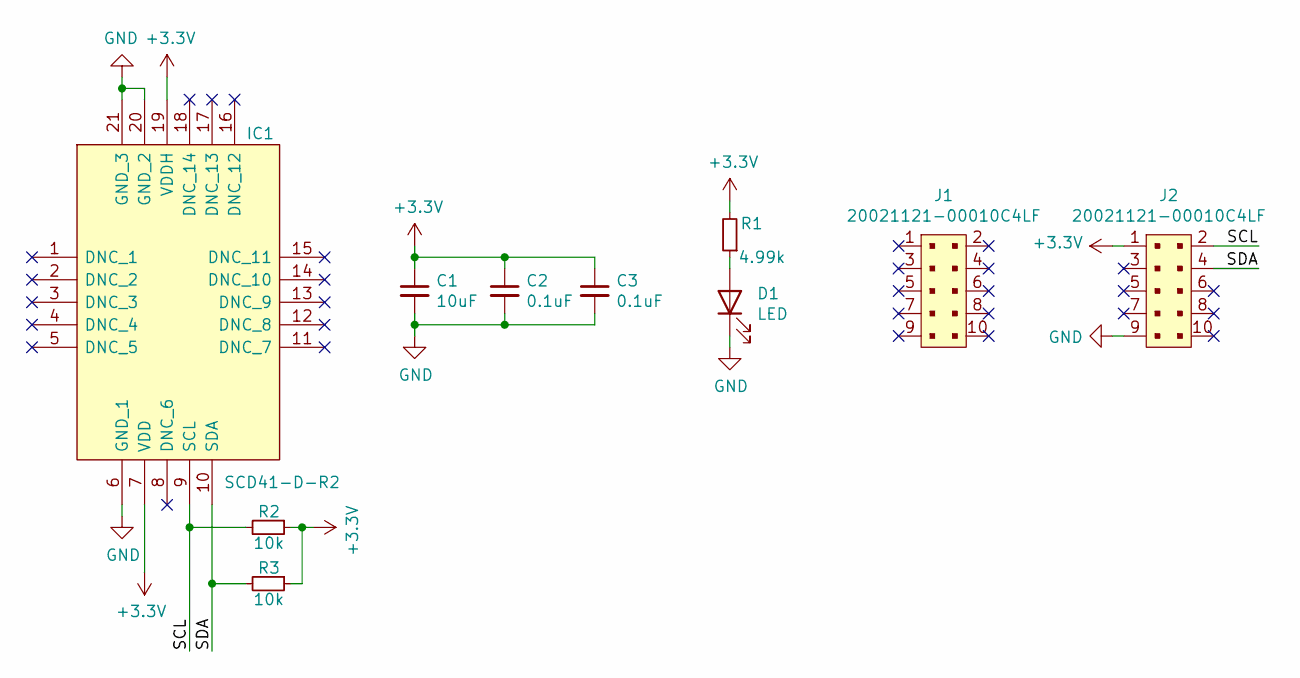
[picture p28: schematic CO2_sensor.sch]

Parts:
C1: 10uF; C_0603_1608Metric_Pad1.08x0.95mm_HandSolder
C2, C3: 0.1uF; C_0603_1608Metric_Pad1.08x0.95mm_HandSolder
D1: LED; LED_0603_1608Metric_Pad1.05x0.95mm_HandSolder
IC1: SCD41-D-R2; SCD41DR2; Manufacturer_Part_Number SCD41-D-R2; Mouser Part Number 403-SCD41-D-R2
J1, J2: 20021121-00010C4LF; PinHeader_2x5_P1.27mm; MPN 20021121-00010C4LF; Digi-Key_PN 609-3695-1-ND
R1: 4.99k; R_0603_1608Metric_Pad0.98x0.95mm_HandSolder
R2, R3: 10k; R_0603_1608Metric_Pad0.98x0.95mm_HandSolder

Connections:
+3V3: C1.1, C2.1, C3.1, IC1.7 (VDD), IC1.19 (VDDH), J2.1, R1.2, R2.1, R3.1
/SCL: IC1.9 (SCL), J2.2, R2.2
/SDA: IC1.10 (SDA), J2.4, R3.2
GND: C1.2, C2.2, C3.2, D1.1 (K), IC1.6 (GND_1), IC1.20 (GND_2), IC1.21 (GND_3), J2.9
unnamed: D1.2 (A), R1.1

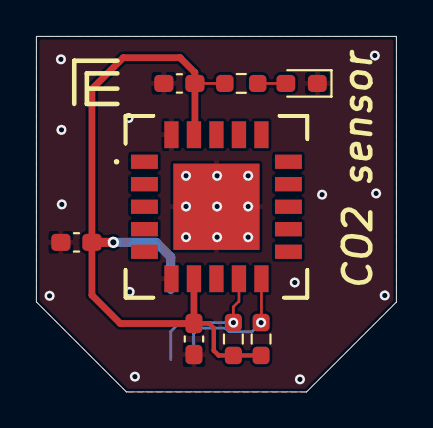
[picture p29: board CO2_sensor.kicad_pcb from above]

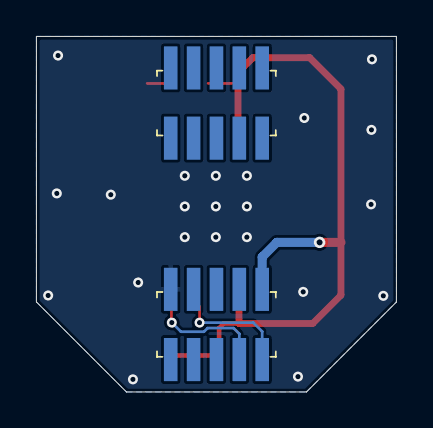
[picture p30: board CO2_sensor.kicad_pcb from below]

Board: 2 copper layers, 20.0 x 19.8 mm, 10 parts (2 on the bottom side), 5 nets.

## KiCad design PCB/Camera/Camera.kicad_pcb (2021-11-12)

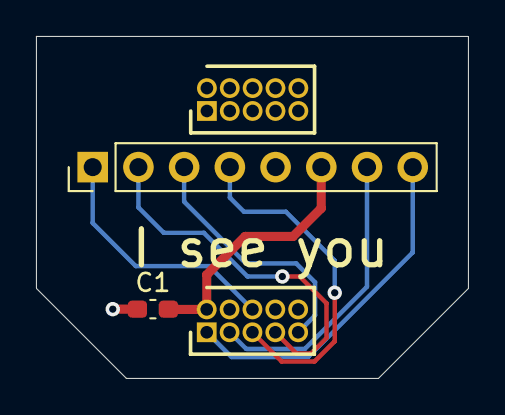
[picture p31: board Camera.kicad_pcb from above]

Board: 2 copper layers, 24.0 x 19.0 mm, 4 parts (0 on the bottom side), 8 nets.

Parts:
C1: 0.1uF; C_0603_1608Metric_Pad1.08x0.95mm_HandSolder
J1, J2: GRPB052VWVN-RC; HDRV10W50P127_2X5_635X340X430P
U1: Arducam_OV2640_module; PinHeader_1x08_P2.54mm_Vertical

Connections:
+3V3: C1.1, J1.2, U1.6
/CS: J1.6, U1.1
/MISO: J1.9, U1.3
/MOSI: J1.7, U1.2
/SCK: J1.5, U1.4
/SCL: J1.1, U1.8
/SDA: J1.3, U1.7
GND: C1.2, J1.10, U1.5

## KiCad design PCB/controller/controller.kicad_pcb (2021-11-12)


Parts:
H1, H2, H3, H4: MountingHole; MountingHole_2.2mm_M2
J1: Conn_01x12_Female; PinHeader_1x12_P2.54mm_Vertical
J2: Conn_01x16_Female; PinHeader_1x16_P2.54mm_Vertical
J3: Conn_01x16_Female; PinHeader_1x16_P2.54mm_Horizontal
U1: Adafruit_Feather_nRF52840; Adafruit_feather_nRF52840

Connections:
/3V: J2.2, J3.2, U1.14 (3V)
/A0: J2.5, J3.3, U1.17 (A0)
/A1: J2.6, J3.4, U1.18 (A1)
/A2: J2.7, J3.5, U1.19 (A2)
/A3: J2.8, J3.6, U1.20 (A3)
/A4: J2.9, J3.7, U1.21 (A4)
/A5: J2.10, J3.8, U1.22 (A5)
/Aref: J2.3, U1.15 (Aref)
/Bat: J1.12, U1.12 (Bat)
/D2: J2.16, J3.9, U1.28 (D2)
/D5: J1.3, J3.10, U1.3 (D5)
/D6: J1.4, J3.11, U1.4 (D6)
/D9: J1.5, J3.12, U1.5 (D9)
/D10: J1.6, J3.13, U1.6 (D10)
/D11: J1.7, J3.14, U1.7 (D11)
/D12: J1.8, J3.15, U1.8 (D12)
/D13: J1.9, J3.16, U1.9 (D13)
/En: J1.11, U1.11 (En)
/GND: J2.4, J3.1, U1.16 (GND)
/MI: J2.13, U1.25 (MI)
/MO: J2.12, U1.24 (MO)
/RX: J2.14, U1.26 (RX)
/Rst: J2.1, U1.13 (Rst)
/SCK: J2.11, U1.23 (SCK)
/SCL: J1.2, U1.2 (SCL)
/SDA: J1.1, U1.1 (SDA)
/TX: J2.15, U1.27 (TX)
/USB: J1.10, U1.10 (USB)


Board: 2 copper layers, 54.5 x 71.0 mm, 8 parts (0 on the bottom side), 28 nets.

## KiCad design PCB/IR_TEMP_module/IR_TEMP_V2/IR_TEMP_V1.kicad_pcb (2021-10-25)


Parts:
C1: 1uF; C_0402_1005Metric_Pad0.74x0.62mm_HandSolder
C2: 0.01uF; C_0402_1005Metric_Pad0.74x0.62mm_HandSolder
H1, H2, H3: MountingHole; M1.6_mounthole
J1, J2, J3, J4, J5, J6, J7, J8, J9, J10, J11, J12: 1_PIN; 1_pin_SMD_1.5mmx1.0mm
R1, R2, R3: 10k; R_0402_1005Metric_Pad0.72x0.64mm_HandSolder
U1: TPIS_1T_1084

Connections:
+3V3: C1.2, C2.2, J1.1, J7.1, R1.2, R2.2, U1.2 (VDD)
/A1: J5.1, J11.1, U1.6 (A1)
/INT: J6.1, J12.1, R3.2
/INT_TPIS: R3.1, U1.4 (INT)
/SCL: J4.1, J10.1, R2.1, U1.5 (SCL)
/SDA: J3.1, J9.1, R1.1, U1.3 (SDA)
GND: C1.1, C2.1, J2.1, J8.1, U1.1 (GND)



Board: 2 copper layers, 10.0 x 20.0 mm, 21 parts (7 on the bottom side), 7 nets.

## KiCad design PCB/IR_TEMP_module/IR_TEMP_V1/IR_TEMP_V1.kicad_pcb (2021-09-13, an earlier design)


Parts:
C1, C5: 1uF; C_0402_1005Metric_Pad0.74x0.62mm_HandSolder
C2, C3, C4: 0.01uF; C_0402_1005Metric_Pad0.74x0.62mm_HandSolder
C6: 6800pF; C_0603_1608Metric_Pad1.08x0.95mm_HandSolder
IC1: LMP91051MTX_NOPB; SOP65P640X120-14N; Manufacturer_Part_Number LMP91051MTX/NOPB; Mouser Part Number 595-LMP91051MTX/NOPB
J1: GRPB052VWVN-RC; HDRV10W50P127_2X5_635X340X430P; Manufacturer_Part_Number GRPB052VWVN-RC
R1: 100k; R_0402_1005Metric_Pad0.72x0.64mm_HandSolder
R2: 160k; R_0402_1005Metric_Pad0.72x0.64mm_HandSolder
R3: 160k; R_0603_1608Metric_Pad0.98x0.95mm_HandSolder
U1: ZTP-135SR; TO-46-4; Manufacturer_Part_Number ZTP-135SR; Mouser Part Number 527-ZTP-135SR

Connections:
+3V3: C1.2, C2.2, IC1.13 (VIO), IC1.14 (VDD), J1.9, R1.1
/A0: IC1.4 (A0), R3.2
/A1: C6.1, IC1.5 (A1), R3.1
/CMOUT: C3.1, C4.2, C6.2, IC1.3 (CMOUT), U1.4 (GND_THERMOPILE)
/MOSI: IC1.12 (SDIO), J1.4
/SCLK: IC1.11 (SCLK), J1.6
/SPICS: IC1.10 (CSB), J1.5
/Temp_A: C5.1, J1.7, R2.1
/Thermistor: R1.2, U1.3 (THERMISTOR)
GND: C1.1, C2.1, C4.1, C5.2, IC1.6 (GND), J1.1, U1.1 (GND_THERMISTOR)
unnamed: C3.2, IC1.1 (IN1), U1.2 (THERMOPILE)
unnamed: IC1.9 (OUT), R2.2



Board: 2 copper layers, 11.0 x 14.7 mm, 12 parts (3 on the bottom side), 12 nets.

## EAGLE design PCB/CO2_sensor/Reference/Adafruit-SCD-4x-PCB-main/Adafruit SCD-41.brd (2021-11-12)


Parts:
C1, C5: 0.1uF; 0603-NO
C2, C3, C4: 10uF; 0805-NO
CONN3, CONN4: STEMMA_I2C_QT; JST_SH4
D1: GREEN; CHIPLED_0603_NOOUTLINE
FID3, FID4: FIDUCIAL_1MM
JP2: HEADER-1X576MIL; 1X05_ROUND_76
Q2: BSS138; SOT363
R1: 10K; 0603-NO
R3: 10K; RESPACK_4X0603
SJ1, SJ2: SOLDERJUMPER_2WAY; SOLDERJUMPER_2WAY_OPEN_NOPASTE
SJ3: SOLDERJUMPERCLOSED; SOLDERJUMPER_CLOSEDWIRE
U2: AP2112K-3.3; SOT23-5
U$1, U$17, U$19, U$21: MOUNTINGHOLE3.0THIN; MOUNTINGHOLE_3.0_PLATEDTHIN
X1: SCD-41; SCD41

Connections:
3.3V: C1.1, C3.1, JP2.2, Q2.2 (G), Q2.5 (G), R1.1, R3.2 (1), R3.4 (1), SJ1.1, SJ2.1, U2.5 (OUT)
GND: C1.2, C2.2, C3.2, C4.2, C5.2, CONN3.1 (GND), CONN3.MT1 (MT), CONN3.MT2 (MT), CONN4.1 (GND), CONN4.MT1 (MT), CONN4.MT2 (MT), D1.C, JP2.3, U2.2 (GND), X1.6 (GND), X1.20 (GND), X1.P$1 (GND)
unnamed: D1.A, SJ3.1
unnamed: R3.1, R3.3 (1), SJ1.2
unnamed: C4.1, C5.1, SJ2.2, X1.7 (VDD), X1.19 (VDDH)
unnamed: R1.2, SJ3.2
SCL: CONN3.4 (SCL), CONN4.4 (SCL), JP2.4, Q2.6 (D), R3.8 (2)
SCL_3V: Q2.1 (S), R3.7 (2), X1.9 (SCL)
SDA: CONN3.3 (SDA), CONN4.3 (SDA), JP2.5, Q2.3 (D), R3.6 (2)
SDA_3V: Q2.4 (S), R3.5 (2), X1.10 (SDA)
VCC: C2.1, CONN3.2 (V+), CONN4.2 (V+), JP2.1, SJ1.3, SJ2.3, U2.1 (IN), U2.3 (EN)

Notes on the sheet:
I2C Pullups & Shift
STEMMA/I2C Headers
ON LED
Power supply



Board: 2 copper layers, 25.4 x 22.9 mm, 27 parts (5 on the bottom side), 11 nets.

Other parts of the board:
U$22: ADAFRUIT_3.5MM
U$25: PCBFEAT-REV-040
U$30, U$31: STEMMAQT

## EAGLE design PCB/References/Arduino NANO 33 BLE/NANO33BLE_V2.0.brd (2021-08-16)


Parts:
C1: 4n7; 0805-R2013X50N; VOLTAGE 1KV
C2, C5, C8, C9, C12, C21: 100n; 0402-1005X55N
C3, C4: 22u; 0805-R2013X50N
C6, C10: 1n; 0402-1005X55N
C7, C11, C13: 10n; 0402-1005X55N
C14: 4u7; 0402-1005X55N
C15, C16: 1u; 0402-1005X55N
D1: PRTR5V; SOT190P230X110-4N
D2: PMEG6020; SODFL3517X110N
D+: DNP; TP-1.00MM
D-: DNP; TP-1.00MM
DL1: YELLOW; LEDC1608X80N-AK
DL2: GREEN; LEDC1608X80N-AK
DL3: -; SMLP34RGB2W
FD1: DNP; FD-1-1.5
FRAME1: DNP; FRAME
HS-1: HTS221
IC1: MPM3610
J1: -; ZX62-AB-5PA
J3: DNP; 2X03-TP1
JP2, JP3: PINHD-1X15-CASTELLATED; 1X15-CASTELL
L1: BLM18EG101; 0603-1608X90N
LPS-1: LPS22; LPS22H
PB1: PTS820; C&K_PTS820_NO_HOLES
R1: 1M; 0402-1005X55N
R2, R3: 330R; 0402-1005X55N
R4, R5: DNP; 0402-1005X55N
R6: 75k; 0402-1005X55N
R7, R11, R12: 1k; 0402-1005X55N
R8: 24k; 0402-1005X55N
R9: 39k; 0402-1005X55N
R10: 100k; 0402-1005X55N
R13, R14: 4k7; 0402-1005X55N
R15: 22R; 0402-1005X55N
SJ1, SJ2, SJ3, SJ4: DNP; SJ
U1: NINA-B3X
U2: LSM9DS1; LSM9DS1_TEMP_LGA24-8X4
U3: MP34DT06JTR; HCLGA
U4: DNP; SON50P300X200X60-9N-EP160X140
U5: APDS-9960; APDS9960

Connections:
+3V3: C3.1, C8.1, C9.2, C15.1, C21.1, DL3.1 (A), J3.1, JP2.2, R4.2, R5.2, R15.2, SJ4.1, U1.9 (VCCIO), U1.10 (VCC), U4.8 (VCC), U5.5 (A)
AIN0_A5/SCL: JP2.9, U1.18 (GPIO18_A)
AIN1_A7: JP2.11, U1.16 (GPIO16_A)
AIN2_A1: JP2.5, U1.27 (GPIO27_A)
AIN3_A0: JP2.4, U1.25 (GPIO25_A)
AIN4_A6: JP2.10, U1.17 (GPIO17_A)
AIN5_A3: JP2.7, U1.23 (GPIO23_A)
AIN6_A2: JP2.6, U1.24 (GPIO24_A)
AIN7_A4/SDA: JP2.8, U1.20 (GPIO20_A)
APDS_PWR: U1.50 (QSPID0/GPIO50)
AREF: JP2.3
D2: JP3.5, U1.39 (GPIO39)
D3~: JP3.6, U1.21 (GPIO21)
D4: JP3.7, U1.40 (GPIO40)
D5~: JP3.8, U1.22 (GPIO22)
D6~: JP3.9, U1.41 (GPIO41)
D7: JP3.10, SJ2.2, U1.47 (QSPID3/GPIO47)
D8: JP3.11, SJ3.2, U1.48 (QSPID1/GPIO48)
D9~: JP3.12, U1.44 (GPIO44)
D10~: JP3.13, U1.36 (GPIO36)
GND: C1.2, C2.2, C3.2, C4.2, C5.1, C6.1, C7.1, C8.2, C9.1, C10.1, C11.1, C12.1, C13.1, C14.1, C15.2, C16.2, C21.2, DL1.C, DL2.C, HS-1.P$5.GND (GND), IC1.3 (AGND), IC1.12 (GND), IC1.13 (GND), IC1.14 (GND), J1.5, J3.5, JP2.14, JP3.4, LPS-1.3 (RES), LPS-1.5 (SDO/SAO), LPS-1.8 (GND), LPS-1.9 (GND), PB1.1 (3), PB1.2 (3), PB1.3, PB1.4 (3), PB1.5 (1), R1.1, R8.1, R9.1, U1.6 (GND), U1.12 (GND), U1.14 (GND), U1.26 (GND), U1.30 (GND), U1.53 (GND), U1.GND@1 (GND), U1.GND@2 (GND), U1.GND@3 (GND), U1.GND@4 (GND), U1.GND@5 (GND), U1.GND@6 (GND), U1.GND@7 (GND), U1.GND@8 (GND), U1.GND@9 (GND), U1.GND@10 (GND), U1.GND@11 (GND), U1.GND@12 (GND), U2.19 (GND), U2.20 (GND), U3.GND, U3.GND@2 (GND), U3.GND@3 (GND), U3.GND@4 (GND), U4.4 (GND), U5.6 (GND)
INT_APDS: U1.52 (QSPICLK/GPIO52), U5.2 (INT)
LB: R12.1, U1.43 (GPIO43)
LG: R11.1, U1.4 (GPIO4)
LR: R7.1, U1.5 (GPIO5)
MIC_PWR: U1.51 (QSPICS/GPIO51), U3.1 (VDD), U3.2 (LR)
MISO~: JP3.15, U1.34 (GPIO34)
MOSI: JP3.14, U1.35 (GPIO35)
unnamed: C1.1, D1.1, J1.6 (SH), J1.7 (SH), J1.8 (SH), J1.9 (SH), J1.10 (SH), J1.11 (SH), R1.2
unnamed: DL2.A, R2.1
unnamed: DL1.A, R3.1
unnamed: C5.2, U2.24 (C1)
unnamed: IC1.1 (FB), R6.1, R8.2
unnamed: IC1.18 (AAM), R9.2
unnamed: IC1.17 (EN), R10.1
unnamed: C7.2, U2.21 (CAP)
unnamed: U5.3 (LDR), U5.4 (K)
unnamed: R2.2, U1.33 (TRACED3/GPIO33)
unnamed: DL3.3 (BLUE_C), R12.2
unnamed: DL3.2 (RED_C), R7.2
unnamed: DL3.4 (GREEN_C), R11.2
unnamed: JP2.12, SJ1.2
unnamed: C16.1, R15.1, U5.8 (VDD)
unnamed: IC1.7 (OUT), IC1.8 (OUT), IC1.9 (OUT), IC1.20 (OUT), R6.2, SJ4.2
NFC1: SJ2.1, U1.28 (NFC1/GPIO28)
NFC2: SJ3.1, U1.29 (NFC2/GPIO29)
PDMCLK: U1.42 (GPIO42), U3.3 (CLK)
PDMDIN: U1.7 (GPIO7), U3.4 (DOUT)
RESETN: C2.1, J3.6, JP2.13, JP3.3, PB1.6 (2), R5.1, U1.19 (RESETN)
RX: JP3.2, U1.38 (GPIO38)
R_PULLUP: R13.2, R14.2, U1.8 (SWO/TRACE_D0/GPIO8)
SCK: JP2.1, R3.2, U1.1 (GPIO1)
SCL1: HS-1.P$2.SCL/SPC (SCL/SPC), LPS-1.2 (SCL/SPC), R13.1, U1.3 (GPIO3), U2.2 (SCL/SPC), U4.6 (SCL), U5.7 (SCL)
SDA1: HS-1.P$4.SDA/SDI/SDO (SDA/SDI/SDO), LPS-1.4 (SDA/SDI/SDO), R14.1, U1.2 (GPIO2), U2.4 (SDA/SDI/SDO), U4.5 (SDA), U5.1 (SDA)
SWCLK: J3.3, R4.1, U1.11 (SWDCLK)
SWDIO: J3.2, U1.15 (SWDIO)
TX: JP3.1, U1.37 (GPIO37)
USB_N: D1.3, D-.X, J1.2, U1.55 (USB_DM)
USB_P: D1.2, D+.X, J1.3, U1.54 (USB_DP)
VBUS: C10.2, L1.2, SJ1.1, U1.31 (VBUS)
VDD_ENV: C11.2, C12.2, C13.2, C14.2, HS-1.P$1.VDD (VCC), HS-1.P$6.CS (CS), LPS-1.1 (VCCIO), LPS-1.6 (CS), LPS-1.10 (VCC), U1.49 (QSPID2/GPIO49), U2.1 (VDDIO), U2.3 (VDDIO), U2.5 (SDO_A/G), U2.6 (SDO_M), U2.7 (CS_A/G), U2.8 (CS_M), U2.22 (VDD), U2.23 (VDD)
VIN: C4.1, D2.C, IC1.16 (VIN), JP2.15, R10.2
VUSB: C6.2, D1.4, D2.A, J1.1, L1.1

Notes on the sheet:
RESET
Crypto Auth
Arturo Guadalupi
HTS221



Board: 4 copper layers, 43.2 x 17.8 mm, 59 parts (4 on the bottom side), 61 nets.

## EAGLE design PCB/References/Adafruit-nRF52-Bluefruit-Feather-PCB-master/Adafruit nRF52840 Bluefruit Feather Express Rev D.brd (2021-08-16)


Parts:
C1, C2: 22pF; 0603-NO
C3, C4, C10: 0.1uF; 0603-NO
C5, C6, C7, C8, C9: 10uF; 0805-NO
D1: MBR120; SOD-123
D2: RED; CHIPLED_0805_NOOUTLINE
D3: ORANGE; CHIPLED_0805_NOOUTLINE
D4: BLUE; CHIPLED_0805_NOOUTLINE
D+: TPTP10R; TP10R
D-: TPTP10R; TP10R
FID1, FID2: FIDUCIAL_1MM
IC2: GD25Q16; USON8
L1: DNP; _0805MP
LED1: WS2812B3535; LED3535
MDBT1: MDBT50
MS1: FEATHERWING_NODIM
Q3: DMG2305; SOT23-R
R2, R3, R5: 1K; 0603-NO
R4: 4.7K; 0603-NO
R10, R11: 22; 0603-NO
R12: 100K; RESPACK_4X0603
SW1, SW2: KMR2; BTN_KMR2_4.6X2.8
SWC: TPTP12R; TP12R
SWD: TPTP12R; TP12R
TP1: TPTP10R; TP10R
U2: AP2112(3.3V); SOT23-5
U3: MCP73831T-2ACI/OT; SOT23-5
X1: 4u20329; 4UCONN_20329_V2
X2: 2x5 0.05"; 2X05_1.27MM_BOX_POSTS
X3: JSTPH; JSTPH2
Y2: 32.768; XTAL3215

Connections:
3.3V: C3.2, C4.2, C5.2, C8.2, IC2.8 (VCC), L1.1, LED1.2 (VDD), MDBT1.28 (VDD), MDBT1.30 (VDDH), MS1.2 (3V), U2.5 (OUT), X2.1 (VCC)
A0: MDBT1.20 (P0.04/AIN2), MS1.5 (GPIOA0)
A1: MDBT1.21 (P0.05/AIN3), MS1.6 (GPIOA1)
A2: MDBT1.14 (P0.30/AIN6), MS1.7 (GPIOA2)
A3: MDBT1.13 (P0.28/AIN4), MS1.8 (GPIOA3)
A4: MDBT1.11 (P0.02/AIN0), MS1.9 (GPIOA4)
A5: MDBT1.9 (P0.03/AIN1), MS1.10 (GPIOA5)
AREF: C10.2, MDBT1.12 (P0.31/AIN7), MS1.3 (AREF)
D2: MDBT1.54 (P0.10/NFC2), MS1.16 (NC)
D5: MDBT1.25 (P1.08), MS1.19 (GPIO5)
D6: MDBT1.23 (P0.07), MS1.20 (GPIO6)
D9: MDBT1.19 (P0.26), MS1.21 (GPIO9)
D10: MDBT1.16 (P0.27), MS1.22 (GPIO10)
D11: MDBT1.22 (P0.06), MS1.23 (GPIO11)
D12: MDBT1.24 (P0.08), MS1.24 (GPIO12)
D13: MDBT1.26 (P1.09), MS1.25 (GPIO13)
D+: D+.TP, R11.1, X1.D+
D-: D-.TP, R10.1, X1.D-
DCCH: L1.2, MDBT1.31 (DCCH)
EN: MS1.27 (EN), R12.2 (1), U2.3 (EN)
GND: C1.2, C2.2, C3.1, C4.1, C5.1, C6.1, C7.1, C8.1, C9.1, C10.1, D2.C, IC2.4 (VSS), LED1.4 (GND), MDBT1.1 (GND), MDBT1.2 (GND), MDBT1.15 (GND), MDBT1.33 (GND), MDBT1.55 (GND), MS1.4 (GND), R4.2, R5.2, R12.3 (1), R12.8 (2), SW1.A, SW1.A' (P1), SW2.A, SW2.A' (P1), U2.2 (GND), U3.2 (VSS), X1.BASE@1 (GND), X1.BASE@2 (GND), X1.GND, X1.SPRT@1 (GND), X1.SPRT@2 (GND), X1.SPRT@3 (GND), X1.SPRT@4 (GND), X2.3 (GND), X2.5 (GND), X2.7 (KEY), X2.9 (GNDDETECT), X3.1
LED1: MDBT1.8 (P1.15), R2.1
LED2: D4.A, MDBT1.3 (P1.10)
MISO: MDBT1.39 (P0.15), MS1.13 (GPIOMISO)
MOSI: MDBT1.37 (P0.13), MS1.12 (GPIOMOSI)
unnamed: D3.C, R3.1
unnamed: D2.A, R2.2
unnamed: C1.1, MDBT1.17 (P0.00/XL1), Y2.P$1
unnamed: C2.1, MDBT1.18 (P0.01/XL2), Y2.P$2
unnamed: R3.2, U3.1 (STAT)
unnamed: R4.1, U3.5 (PROG)
unnamed: D4.C, R5.1
NEOPIX: LED1.1 (DI), MDBT1.38 (P0.16)
NFC2: MDBT1.52 (P0.09/NFC1), TP1.TP
QSPI_CS: IC2.1 (SSEL), MDBT1.44 (P0.20)
QSPI_DATA0: IC2.5 (MOSI), MDBT1.41 (P0.17)
QSPI_DATA1: IC2.2 (MISO), MDBT1.46 (P0.22)
QSPI_DATA2: IC2.3 (WP#/IO2), MDBT1.45 (P0.23)
QSPI_DATA3: IC2.7 (HOLD#/IO3), MDBT1.43 (P0.21)
QSPI_SCK: IC2.6 (SCK), MDBT1.42 (P0.19)
RESET: MDBT1.40 (P0.18/RESET), MS1.1 (!RESET), SW1.B (S), SW1.B' (S1), X2.10 (NRESET)
RXD: MDBT1.48 (P0.24), MS1.14 (GPIORX)
SCK: MDBT1.36 (P0.14), MS1.11 (GPIOSCK)
SCL: MDBT1.27 (P0.11), MS1.18 (GPIOSCL)
SDA: MDBT1.29 (P0.12), MS1.17 (GPIOSDA)
SWCLK: MDBT1.53 (SWDCLK), SWC.TP, X2.4 (SWDCLK)
SWDIO: MDBT1.51 (SWDIO), SWD.TP, X2.2 (SWDIO)
SWITCH: MDBT1.50 (P1.02), SW2.B (S), SW2.B' (S1)
SWO: MDBT1.47 (P1.00), X2.6 (SWO)
TXD: MDBT1.49 (P0.25), MS1.15 (GPIOTX)
USBD+: MDBT1.35 (D+), R11.2
USBD-: MDBT1.34 (D-), R10.2
VBAT: C9.2, MS1.28 (VBAT), Q3.3 (D), R12.4 (1), U3.3 (VBAT), X3.2
VBUS: C6.2, D1.A, D3.A, MDBT1.32 (VBUS), MS1.26 (USB), Q3.1 (G), R12.1, U3.4 (VDD), X1.VBUS
VDIV: MDBT1.10 (P0.29/AIN5), R12.5 (2), R12.6 (2)
VHI: C7.2, D1.C, Q3.2 (S), R12.7 (2), U2.1 (IN)

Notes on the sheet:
10K = 100mA
5.0K = 200mA
2.0K = 500mA
1.0K = 1000mA
LIPO CHARGING
To charge the LIPO, insert the battery in the JST PH connector and connect USB at the same time.
POWER AND FILTERING (600mA Output)
JST PH LIPO INPUT
Dynamic VIN selection: VBUS (USB) will override VBAT (LIPO) via D5 when both are present.
Dropout Voltage (25°C): 100mA: ~250/~40mV 300mA: ~300/~125mV 600mA: ~375/~260mV
INDICATOR LEDS
RESET/USER SWITCHES
DECOUPLING CAPS
SWD DEBUGGER
16MBIT QSPI FLASH
MICRO USB
NEOPIXEL
Place 10uH for DC/DC



Board: 4 copper layers, 50.8 x 22.9 mm, 45 parts (7 on the bottom side), 56 nets.

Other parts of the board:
U$10: PCBFEAT-REV-056
U$12: NRF52840_BOT
U$14: NRF52840_TOP

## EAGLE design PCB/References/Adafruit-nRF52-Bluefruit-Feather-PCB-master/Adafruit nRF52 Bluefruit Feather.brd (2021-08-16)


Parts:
C1, C2: 22pF; 0603-NO
C3: 10uF; 0805-NO
C4: 1uF; 0603-NO
C5, C6, C8: 10µF; 0805-NO
C7: 10uf; 0805-NO
C9, C13: 300pF; _0603MP
C10, C11: 0.1uF; 0603-NO
C12: 1nF; 0603-NO
CHG: ORANGE; CHIPLED_0805_NOOUTLINE
D1: RED; CHIPLED_0805_NOOUTLINE
D2: BLUE; CHIPLED_0805_NOOUTLINE
D4: 1N4148; SOD-323
D5: MBR120; SOD-123
FID1, FID3: FIDUCIAL_1MM
JP1, JP2: HEADER-1X12MM; 1X01_2MM
L2: 10uH; 0805-NO
MS1: FEATHERWING_NODIM
Q3: DMG3415U-7; SOT23-R
R1, R2, R3, R9: 1K; 0603-NO
R4: 806K; 0603-NO
R5: 100K; 0603-NO
R6: 2M; 0603-NO
R7, R8: 10K; 0603-NO
R12: 100k; 0603-NO
SJ2: BAT; SOLDERJUMPER_CLOSEDWIRE
SW1, SW2: KMR2; BTN_KMR2_4.6X2.8
TP2: FRST; PAD-1.5X2.0
TP3, TP4: TESTPOINTROUND2MM; TESTPOINT_ROUND_2MM
U1: MDBT42; BLE_MODULE_RAYTAC_MDBT42
U2: AP2112(3.3V); SOT23-5
U3: MCP73831T-2ACI/OT; SOT23-5
U4: CP2104; QFN24_4MM_SMSC
X1: 4u20317; 2X05_1.27MM_BOX_POSTS
X2: JSTPH; JSTPH2
X3: 4u20329; 4UCONN_20329_V2
X4: 32.768; XTAL3215

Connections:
3.3V: C3.1, C8.1, C10.1, D4.C, MS1.2 (3V), MS1.3 (AREF), R7.2, U1.11 (VDD), U2.5 (OUT), U4.5 (VIO), U4.6 (VDD), U4.7 (REGIN), X1.1 (VCC)
A0/0.02: MS1.5 (GPIOA0), U1.15 (P0.02/AIN0)
A1/0.03: MS1.6 (GPIOA1), U1.16 (P0.03/AIN1)
A2/0.04: MS1.7 (GPIOA2), U1.17 (P0.04/AIN2)
A3/0.05: MS1.8 (GPIOA3), U1.18 (P0.05/AIN3)
A4/0.28: MS1.9 (GPIOA4), U1.5 (P0.28/AIN4)
A5/0.29: MS1.10 (GPIOA5), U1.6 (P0.29/AIN5)
A6/P0.30: MS1.20 (GPIO6), U1.7 (P0.30/AIN6)
A7/P0.31: C12.1, MS1.21 (GPIO9), R4.2, R6.1, U1.8 (P0.31/AIN7)
DFU: MS1.16 (NC), SW2.B (S), SW2.B' (S1), U1.34 (P0.20)
DTR: C11.2, U4.23 (DTR)
EN: MS1.27 (EN), R5.1, U2.3 (EN)
FRST: TP2.P$1, U1.38 (P0.22)
GND: C1.2, C2.2, C3.2, C4.2, C5.2, C6.2, C7.2, C8.2, C9.2, C10.2, C12.2, C13.2, D1.C, D2.C, MS1.4 (GND), R6.2, R8.2, R12.1, SW1.B (S), SW1.B' (S1), SW2.A, SW2.A' (P1), U1.1 (GND), U1.12 (GND), U1.24 (GND), U1.39 (GND), U2.2 (GND), U3.2 (VSS), U4.2 (GND), U4.THERM (TP), X1.3 (GND), X1.5 (GND), X1.7 (KEY), X1.9 (GNDDETECT), X2.1, X3.BASE@1 (GND), X3.BASE@2 (GND), X3.GND, X3.SPRT@1 (GND), X3.SPRT@2 (GND), X3.SPRT@3 (GND), X3.SPRT@4 (GND)
LED1: R1.2, U1.31 (P0.17)
LED2: R2.2, U1.33 (P0.19)
MISO: MS1.13 (GPIOMISO), U1.28 (P0.14)
MOSI: MS1.12 (GPIOMOSI), U1.27 (P0.13)
unnamed: C1.1, U1.13 (P0.00/XL1), X4.P$1
unnamed: C2.1, U1.14 (P0.01/XL2), X4.P$2
unnamed: L2.2, U1.10 (DCC)
unnamed: CHG.C, R3.1
unnamed: D1.A, R1.1
unnamed: D2.A, R2.1
unnamed: C4.1, L2.1, U1.9 (DEC4)
unnamed: R3.2, U3.1 (STAT)
unnamed: R8.1, U3.5 (PROG)
unnamed: R9.1, U4.21 (TXD)
unnamed: C11.1, SJ2.2
unnamed: C7.1, U4.16 (VPP)
P0.07: MS1.23 (GPIO11), U1.20 (P0.07)
P0.09/NFC1: C13.1, JP2.1, U1.22 (P0.09)
P0.10/NFC2: C9.1, JP1.1, U1.23 (P0.10)
P0.11: MS1.22 (GPIO10), U1.25 (P0.11)
P0.15: MS1.24 (GPIO12), U1.29 (P0.15)
P0.16: MS1.25 (GPIO13), U1.30 (P0.16)
P0.27: MS1.19 (GPIO5), U1.4 (P0.27)
RESET: D4.A, MS1.1 (!RESET), R7.1, SJ2.1, SW1.A, SW1.A' (P1), U1.35 (P0.21/RESET), X1.10 (NRESET)
RXD: MS1.14 (GPIORX), R9.2, U1.21 (P0.08)
SCK: MS1.11 (GPIOSCK), U1.26 (P0.12)
SCL: MS1.18 (GPIOSCL), U1.3 (P0.26)
SDA: MS1.17 (GPIOSDA), U1.2 (P0.25)
SWCLK: TP4.P$1, U1.36 (SWDCLK), X1.4 (SWDCLK)
SWDIO: TP3.P$1, U1.37 (SWDIO), X1.2 (SWDIO)
SWO: U1.32 (P0.18/SWO), X1.6 (SWO)
TXD: MS1.15 (GPIOTX), U1.19 (P0.06), U4.20 (RXD)
USBD+: U4.3 (D+), X3.D+
USBD-: U4.4 (D-), X3.D-
VBAT: C5.1, MS1.28 (VBAT), Q3.3 (D), R4.1, U3.3 (VBAT), X2.2
VBUS: CHG.A, D5.A, MS1.26 (USB), Q3.1 (G), R12.2, U3.4 (VDD), U4.8 (VBUS), X3.VBUS
VIN: C6.1, D5.C, Q3.2 (S), R5.2, U2.1 (IN)

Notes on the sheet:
10K = 100mA
5.0K = 200mA
2.0K = 500mA
1.0K = 1000mA
LIPO CHARGING
LIPO MONITORING
To charge the LIPO, insert the battery in the JST PH connector and connect USB at the same time.
POWER AND FILTERING (600mA Output)
JST PH LIPO INPUT
Dynamic VIN selection: VBUS (USB) will override VBAT (LIPO) via D5 when both are present.
Dropout Voltage (25°C): 100mA: ~250/~40mV 300mA: ~300/~125mV 600mA: ~375/~260mV
USB POWER
USB/TTL Bridge
Adafruit Feather Pinout
See: https://devzone.nordicsemi.com/blogs/943/measuring-lithium-battery-voltage-with-nrf52/ Maximum voltage: 4.2 V * (2 M/(0.8 M+2 M)) = 3 V Minimum voltage: 2.7 V * (2 M/(0.8 M+2 M)) = 1.93 V ADC value at 4.2 V - 12 bit setup: 3 V * (1/5) / 0.6 V * 4095 = 4095 ADC value at 2.7 V - 12 bit setup: 1.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
USB RESET (DTR)
0.1uF+10K @ 3.3V = ~1.2ms to 0.7VCC



Board: 2 copper layers, 50.8 x 22.9 mm, 54 parts (8 on the bottom side), 51 nets.

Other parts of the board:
U$17: PCBFEAT-REV-040
U$45: BLUEFRUITLOGO_100MM
U$46: FEATHERLOGO_MED
U$47: ADAFRUIT_5MM
U$49: ADAFRUIT_3.5MM

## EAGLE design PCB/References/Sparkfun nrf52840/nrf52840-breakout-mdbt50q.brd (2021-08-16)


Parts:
C1, C4: 10uF; 0603
C2: 0.1uF; 0603
C3, C7: 15pF; 0603
C5, C6: 4.7uF; 0603
C8, C9: 1.0uF; 0603
C10, C11: DNP; 0603
D1: BLUE; LED-0603
D2: Yellow; LED-0603
D3, D4: 1A/23V/620mV; SOD-323
D6: RED; LED-0603
FD1, FD2, FD3, FD4: FIDUCIALUFIDUCIAL; FIDUCIAL-MICRO
FRAME1: FRAME-LETTER; CREATIVE_COMMONS
J1: JST_2MM_MALESMD; JST-2-SMD
J2, J13: CONN_12NO_SILK; 1X12_NO_SILK
J3: QWIIC_CONNECTORJS-1MM; 1X04_1MM_RA
J4, J5, J12, J14: CONN_021X02_NO_SILK; 1X02_NO_SILK
J6: USB_MICRO-B_HALF_PTH_MILL; USB-MICROB-PTH-MILL
J7, J9: CONN_07NO_SILK; 1X07_NO_SILK
J8: CORTEX_DEBUG_PTH; 2X5-PTH-1.27MM
LOGO1: SFE_LOGO_NAME.2_INCH; SFE_LOGO_NAME_.2
LOGO2: OSHW-LOGOS; OSHW-LOGO-S
R1, R2: 27; 0603
R3, R6, R10: 1k; 0603
R4, R7: 10k; 0603
R5: 2.0k; 0603
R8, R9: 2.2k; 0603
S1: RESET; TACTILE_SWITCH_SMD_RIGHT_ANGLE
S2: SWITCH-SPDT-SMD-RIGHT-ANGLE; SWITCH_SPST_SMD_A
S3: BOOTLOAD; TACTILE_SWITCH_SMD_RIGHT_ANGLE
U1: MDBT50Q
U2: MCP73831; SOT23-5
U3: 3.3V; SOT23-5
Y1: 32.768kHz; CRYSTAL-SMD-3.2X1.5MM

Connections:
3.3V: C1.1, C2.1, C4.1, C9.1, J2.9, J3.2, J8.1 (VCC), R4.2, R7.2, R8.2, R9.2, R10.2, U1.28 (VDD), U1.30 (VDDH), U3.5 (OUT)
!RESET: J2.10, J8.10 (!RESET), R4.1, S1.2, U1.40 (P0.18(NRESET))
D+: R1.2, U1.35 (D+)
D+_CON: J6.D+, R1.1
D-: R2.2, U1.34 (D-)
D-_CON: J6.D-, R2.1
GND: C1.2, C2.2, C3.1, C4.2, C5.2, C6.2, C7.1, C8.2, C9.2, C10.2, C11.2, D1.C, D6.C, J1.1 (-), J2.11, J3.1, J6.GND, J8.3 (GND), J8.5 (GND), J8.9 (GNDDTCT), J9.1, J9.2, J9.3, J9.4, J9.5, J9.6, J9.7, J12.1, J13.1, J13.2, J13.3, J13.4, J13.5, J13.6, J13.7, J13.8, J13.9, J13.10, J13.11, J13.12, J14.1, J14.2, R5.1, S1.1, S2.1 (O), S3.1, U1.1 (GND), U1.2 (GND), U1.15 (GND), U1.33 (GND), U1.55 (GND), U2.2 (VSS), U3.2 (GND)
unnamed: R5.2, U2.5 (PROG)
unnamed: D2.C, R6.2
unnamed: R6.1, U2.1 (STAT)
unnamed: D1.A, R3.1
unnamed: D6.A, R10.1
P0.02/AIN0: J2.1, U1.11 (P0.02(AIN0))
P0.03/AIN1: J2.2, U1.9 (P0.03(AIN1))
P0.04/AIN2: J2.8, U1.20 (P0.04(AIN2))
P0.05/AIN3: J2.7, U1.21 (P0.05(AIN3))
P0.06: U1.22 (P0.06)
P0.07: R3.2, U1.23 (P0.07(TRACECLK))
P0.08: J3.3, R8.1, U1.24 (P0.08)
P0.09/NFC1: C11.1, J7.2, U1.52 (P0.09(NFC1))
P0.10/NFC2: C10.1, J7.1, U1.54 (P0.10(NFC2))
P0.11: J3.4, R9.1, U1.27 (P0.11(TRACEDATA2))
P0.13: R7.1, S3.2, U1.37 (P0.13)
P0.15: J5.1, U1.39 (P0.15)
P0.17: J5.2, U1.41 (P0.17)
P0.19: J7.7, U1.42 (P0.19)
P0.20: J7.6, U1.44 (P0.20)
P0.21: J7.5, U1.43 (P0.21)
P0.22: J7.4, U1.46 (P0.22)
P0.23: J7.3, U1.45 (P0.23)
P0.28/AIN4: J2.6, U1.13 (P0.28(AIN4))
P0.29/AIN5: J2.5, U1.10 (P0.29(AIN5))
P0.30/AIN6: J2.4, U1.14 (P0.30(AIN6))
P0.31/AIN7: J2.3, U1.12 (P0.31(AIN7))
SHIELD: J6.SHIELD, J6.SHIELD2 (SHIELD), J6.SHIELD3 (SHIELD), J6.SHIELD4 (SHIELD), J6.SHIELD5 (SHIELD), J6.SHIELD6 (SHIELD), J6.SHIELD7 (SHIELD), J6.SHIELD8 (SHIELD), J6.SHIELD9 (SHIELD), J6.SHIELD10 (SHIELD)
SWDCLK: J4.2, J8.4 (SWDCLK/TCK), U1.53 (SWDCLK)
SWDIO: J4.1, J8.2 (SWDIO/TMS), U1.51 (SWDIO)
VIN: C8.1, D3.C, D4.C, J2.12, S2.3 (S), U3.1 (IN)
VREG_EN: S2.2, U3.3 (EN)
V_BATT: C6.1, D4.A, J1.2 (+), J12.2, U2.3 (VBAT)
V_USB: C5.1, D2.A, D3.A, J6.VBUS, U1.32 (VBUS), U2.4 (VIN)
XL1: C3.2, U1.17 (P0.00(XL1)), Y1.P$2 (2)
XL2: C7.2, U1.18 (P0.01(XL2)), Y1.P$1 (1)

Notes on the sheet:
v10
Jim Lindblom
SWD Program/Debug Interface
I2C/Qwiic
Headers
NFC Capacitors (DNP)
Buttons
User LED
nRF52840 (MDBT50Q)
USB/LiPo Charger
Power Source Select
3.3V Regulator
Unpopulated NFC caps: External caps to tune antenna resonance to 13.56MHz. Recommended: 130pF
nRF52840 VCC Range: 2.5V - 3.6V



Board: 2 copper layers, 47.0 x 22.9 mm, 110 parts (37 on the bottom side), 42 nets.

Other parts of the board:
U$1: 3V316
U$2: 130
U$3: RST19
U$4: ON1
U$5: CHG26
U$6: PWR27
U$7: GND17
U$8: QWIIC#LOGO#JPG
U$9: 20
U$10: 31
U$11: 292
U$12: 313
U$13: 3V30
U$14: 285
U$15: 521
U$16: 421
U$17: HTTP###SFE#IO#T8200
U$18: #RST6
U$19: GND7
U$20: VIN8
U$21: 1022
U$22: 916
U$23: 2111
U$24: 1912
U$25: 1713
U$26: 1522
U$27: VIN19
U$28: 70
U$29: NRF52840_MINI_BREAKOUT0
U$30: GND6
U$31: 27
U$32: 36
U$33: SWD0
U$34: 315
U$35: 300
U$36: 301
U$37: 293
U$38: 108
U$39: 51
U$40: 40
U$41: 97
U$42: 236
U$43: 200
U$44: 225
U$45: 221
U$46: 214
U$47: 203
U$48: 192
U$49: 151
U$50: 170
U$51: RST1
U$52: ANALOG2
U$53: 232
U$54: SCL#114
U$55: SDA#83
U$56: IO2
U$57: CLK1
U$58: OFF2

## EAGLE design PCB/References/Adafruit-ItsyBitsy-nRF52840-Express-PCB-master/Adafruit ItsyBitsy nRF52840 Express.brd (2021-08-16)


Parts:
C1, C2: 22pF; _0603MP
C3, C4: 0.1uF; 0603-NO
C5, C7, C8: 10uF; 0805-NO
D1, D3: MBR120; SOD-123
D2: RED; CHIPLED_0805_NOOUTLINE
D+: TPTP10R; TP10R
D-: TPTP10R; TP10R
FID1, FID2, FID3, FID4: FIDUCIAL_1MM
IC1: 74HCT1G125DBV; SOT23-5
IC2: GD25Q16; USON8
JP2, JP4: HEADER-1X14; 1X14_ROUND70
L2: AP102-2020; APA102_2020
MDBT1: MDBT50
R1: 10K; 0603-NO
R2: 1K; 0603-NO
R10, R11: 22; 0603-NO
SW1, SW2: KMR2; BTN_KMR2_4.6X2.8
SWC: TPTP13R; TP13R
SWD: TPTP13R; TP13R
U2: AP2112(3.3V); SOT23-5
X1: 4u20329; 4UCONN_20329_V2
Y2: 32.768; XTAL3215

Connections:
3.3V: C3.2, C4.2, C5.2, C8.2, IC2.8 (VCC), JP4.13, L2.3 (VDD), MDBT1.28 (VDD), MDBT1.30 (VDDH), U2.5 (OUT)
!RESET: JP4.14, MDBT1.40 (P0.18/RESET), SW1.B (S), SW1.B' (S1)
A0: JP4.10, MDBT1.20 (P0.04/AIN2)
A1: JP4.9, MDBT1.14 (P0.30/AIN6)
A2: JP4.8, MDBT1.13 (P0.28/AIN4)
A3: JP4.7, MDBT1.12 (P0.31/AIN7)
A4: JP4.6, MDBT1.11 (P0.02/AIN0)
A5: JP4.5, MDBT1.9 (P0.03/AIN1)
D2: JP4.1, MDBT1.50 (P1.02)
D5: IC1.2 (I), MDBT1.16 (P0.27)
D5_5V: IC1.4 (O), JP2.10
D7: JP2.9, MDBT1.25 (P1.08)
D9: JP2.8, MDBT1.23 (P0.07)
D10: JP2.7, MDBT1.21 (P0.05/AIN3)
D11: JP2.6, MDBT1.19 (P0.26)
D12: JP2.5, MDBT1.27 (P0.11)
D13: JP2.4, MDBT1.29 (P0.12)
D+: D+.TP, R11.1, X1.D+
D-: D-.TP, R10.1, X1.D-
DCCH: MDBT1.31 (DCCH)
DOT_CLK: L2.5 (CKI), MDBT1.26 (P1.09)
DOT_DATA: L2.6 (DI), MDBT1.24 (P0.08)
EN: JP4.12, R1.1, U2.3 (EN)
GND: C1.2, C2.2, C3.1, C4.1, C5.1, C7.1, C8.1, IC1.1 (OE), IC1.3 (GND), IC2.4 (VSS), JP2.2, L2.4 (GND), MDBT1.1 (GND), MDBT1.2 (GND), MDBT1.15 (GND), MDBT1.33 (GND), MDBT1.55 (GND), R2.2, SW1.A, SW1.A' (P1), SW2.A, SW2.A' (P1), U2.2 (GND), X1.BASE@1 (GND), X1.BASE@2 (GND), X1.GND, X1.SPRT@1 (GND), X1.SPRT@2 (GND), X1.SPRT@3 (GND), X1.SPRT@4 (GND)
LED1: D2.A, MDBT1.22 (P0.06)
MISO: JP4.2, MDBT1.44 (P0.20)
MOSI: JP4.3, MDBT1.39 (P0.15)
unnamed: D2.C, R2.1
unnamed: C1.1, MDBT1.17 (P0.00/XL1), Y2.P$1
unnamed: C2.1, MDBT1.18 (P0.01/XL2), Y2.P$2
QSPI_CS: IC2.1 (SSEL), MDBT1.45 (P0.23)
QSPI_DATA0: IC2.5 (MOSI), MDBT1.43 (P0.21)
QSPI_DATA1: IC2.2 (MISO), MDBT1.46 (P0.22)
QSPI_DATA2: IC2.3 (WP#/IO2), MDBT1.47 (P1.00)
QSPI_DATA3: IC2.7 (HOLD#/IO3), MDBT1.41 (P0.17)
QSPI_SCK: IC2.6 (SCK), MDBT1.42 (P0.19)
RX_D0: JP2.14, MDBT1.49 (P0.25)
SCK: JP4.4, MDBT1.37 (P0.13)
SCL: JP2.11, MDBT1.36 (P0.14)
SDA: JP2.12, MDBT1.38 (P0.16)
SWCLK: MDBT1.53 (SWDCLK), SWC.TP
SWDIO: MDBT1.51 (SWDIO), SWD.TP
SWITCH: MDBT1.10 (P0.29/AIN5), SW2.B (S), SW2.B' (S1)
TX_D1: JP2.13, MDBT1.48 (P0.24)
USBD+: MDBT1.35 (D+), R11.2
USBD-: MDBT1.34 (D-), R10.2
VBAT: D3.A, JP2.1
VBUS: D1.A, JP2.3, MDBT1.32 (VBUS), X1.VBUS
VHI: C7.2, D1.C, D3.C, IC1.5 (VCC), JP4.11, R1.2, U2.1 (IN)

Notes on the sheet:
POWER AND FILTERING (600mA Output)
Dropout Voltage (25°C): 100mA: ~250/~40mV 300mA: ~300/~125mV 600mA: ~375/~260mV
INDICATOR LEDS
RESET/USER SWITCHES
DECOUPLING CAPS
SWD DEBUGGER
16MBIT QSPI FLASH
MICRO USB
Place 10uH for DC/DC



Board: 2 copper layers, 35.6 x 17.8 mm, 36 parts (17 on the bottom side), 48 nets.

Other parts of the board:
U$12: ITSYNRF52840_TOP
U$14: ITSYNRF52840_BOT
U$15: PCBFEAT-REV-040

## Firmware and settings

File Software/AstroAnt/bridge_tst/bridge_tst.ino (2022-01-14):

/*********************************************************************
 This is an example for our nRF52 based Bluefruit LE modules

 Pick one up today in the adafruit shop!

 Adafruit invests time and resources providing this open source code,
 please support Adafruit and open-source hardware by purchasing
 products from Adafruit!

 MIT license, check LICENSE for more information
 All text above, and the splash screen below must be included in
 any redistribution
*********************************************************************/
#include <Adafruit_MPU6050.h>
#include <Adafruit_Sensor.h>
#include <SPI.h>
#include <Wire.h>
#include <bluefruit.h>
#include <Adafruit_LittleFS.h>
#include <InternalFileSystem.h>
#include "NRF52TimerInterrupt.h"
#include "NRF52_ISR_Timer.h"

// BLE Service
BLEDfu  bledfu;  // OTA DFU service
BLEDis  bledis;  // device information
BLEUart bleuart; // uart over ble
BLEBas  blebas;  // battery

char* devece_name = "BridgeAnt";

const int msg_bye_cnt = 20;

const int motor_speed = 200;

const uint8_t node_address = 0x04;

// Data for test
uint8_t reply_buf[20]     = {0xEB,0x9F,node_address,0x00,0x00,0x00,0x00,0x00,0x00,0x00,0x00,0x00,0x00,0x00,0x00,0x00,0x00,0x00,0x00,0x00};
// ACK frame
uint8_t start_ack_buf[20] = {0xEB,0x90,node_address,0xAA,0xAA,0x00,0x00,0x00,0x00,0x00,0x00,0x00,0x00,0x00,0x00,0x00,0x00,0x00,0x00,0x00};
uint8_t cali_ack_buf[20]  = {0xEB,0x90,node_address,0x11,0xAA,0x00,0x00,0x00,0x00,0x00,0x00,0x00,0x00,0x00,0x00,0x00,0x00,0x00,0x00,0x00};
uint8_t stop_ack_buf[20]  = {0xEB,0x90,node_address,0xEE,0xAA,0x00,0x00,0x00,0x00,0x00,0x00,0x00,0x00,0x00,0x00,0x00,0x00,0x00,0x00,0x00};
uint8_t err_ack_buf[20]   = {0xEB,0x90,node_address,0xFF,0xAA,0x00,0x00,0x00,0x00,0x00,0x00,0x00,0x00,0x00,0x00,0x00,0x00,0x00,0x00,0x00};

uint8_t recv_msg[msg_bye_cnt+1] = {0};

int start_cmd_flag = 0;
int stop_cmd_flag = 0;
int cali_cmd_flag = 0;
int cali_done_flag = 0;
int error_cmd_flag = 0;

uint8_t recv_cmd = 0;

const int batt_pin = A0;
int batt_v = 0;
int battValue = 0;
uint8_t batt_level = 0x00;
uint8_t counter = 0;

// =========== MPU6050 ===========
Adafruit_MPU6050 mpu;

// =========== interrupt parameter ===========
#define HW_TIMER_INTERVAL_MS 1

NRF52Timer ITimer(NRF_TIMER_1);
NRF52_ISR_Timer ISR_Timer;

// interrupt interval: send back data every 50ms
#define TIMER_INTERVAL_50ms 50L
bool timer4Interrupt = false;

void TimerHandler()
{
  ISR_Timer.run();
}

// ========= PID parameters ==========
/* IMU Data */
float gyroZangle = 0.0;     // Angle calculate using the gyro only
float gyroZangle_pre = 0.0; // Angle calculate using the gyro only

float dev_Xangle = 0.0;
float dev_Yangle = 0.0;
float dev_Zangle = 0.0;

float gyroXrate = 0.0;
float gyroYrate = 0.0;
float gyroZrate = 0.0;

float accelx = 0.0;
float accely = 0.0;
float accelz = 0.0;

float yy = 0;
float yy_acc = 0;
float yy_pre = 0;
float dev_yy = 0;

// Play with the PID parameters
float tau_p = 50;
float tau_d = 10;
float tau_i = 1;

// Encoder counter
uint16_t encoder1Counter = 0;
uint16_t encoder2Counter = 0;

uint8_t encoder1Counter_pre = 0;
uint8_t encoder2Counter_pre = 0;

signed char dev_encoder1Counter = 0;
signed char dev_encoder2Counter = 0;

const int cali_data_len = 40; // accumulate 2s of IMU data for calibration.

float shift_reg_x[cali_data_len] = {0};
float shift_reg_y[cali_data_len] = {0};
float shift_reg_z[cali_data_len] = {0};

uint32_t timer = 0;

int i = 0;
int ii = 0;

float cali_sum_x = 0.0;
float cali_x = 0.0;

float cali_sum_y = 0.0;
float cali_y = 0.0;

float cali_sum_z = 0.0;
float cali_z = 0.0;

float cali_bias_x = 0.0;
float cali_bias_y = 0.0;
float cali_bias_z = 0.0;

int ix = 0;
int iy = 0;
int iz = 0;
int ig = 0;

int steer = 0;
float steer_f = 0.0;

// int overflow_flag = 0;

// ========== SVD ==========
float aa = 1.6924895;
float bb = 6.1480306;

void setup()
{
  // Serial.begin(115200);
  // while (!Serial);

  // Serial.println("BLE_GATT_ATT_MTU_DEFAULT = ");
  // Serial.println(BLE_GATT_ATT_MTU_DEFAULT);

  pinMode(LED_RED, OUTPUT);

  pinMode(M1_IN1, OUTPUT);
  pinMode(M1_IN2, OUTPUT);
  pinMode(M2_IN1, OUTPUT);
  pinMode(M2_IN2, OUTPUT);

  pinMode(Encoder_A1, INPUT);
  pinMode(Encoder_A2, INPUT);

  attachInterrupt(Encoder_A1, ENC1_INT_Routine, RISING);
  attachInterrupt(Encoder_A2, ENC2_INT_Routine, RISING);

  // Setup the BLE LED to be enabled on CONNECT
  // Note: This is actually the default behavior, but provided
  // here in case you want to control this LED manually via PIN 19
  Bluefruit.autoConnLed(true);

  // Config the peripheral connection with maximum bandwidth 
  // more SRAM required by SoftDevice
  // Note: All config***() function must be called before begin()
  Bluefruit.configPrphBandwidth(BANDWIDTH_MAX);

  Bluefruit.begin();
  Bluefruit.setTxPower(4);    // Check bluefruit.h for supported values
  //Bluefruit.setName(getMcuUniqueID()); // useful testing with multiple central connections
  Bluefruit.setName(devece_name);
  Bluefruit.Periph.setConnectCallback(connect_callback);
  Bluefruit.Periph.setDisconnectCallback(disconnect_callback);

  // To be consistent OTA DFU should be added first if it exists
  bledfu.begin();

  // Configure and Start Device Information Service
  bledis.setManufacturer("Adafruit Industries");
  bledis.setModel("Bluefruit Feather52");
  bledis.begin();

  // Configure and Start BLE Uart Service
  bleuart.begin();

  // Start BLE Battery Service
  blebas.begin();
  blebas.write(10);

  // Set up and start advertising
  startAdv();

  // Serial.println("Please use Adafruit's Bluefruit LE app to connect in UART mode");
  // Serial.println("Once connected, enter character(s) that you wish to send");

  // ============== Interrupt ==============
  // Interval in microsecs
  ITimer.attachInterruptInterval(HW_TIMER_INTERVAL_MS * 1000, TimerHandler);

  // Just to demonstrate, don't use too many ISR Timers if not absolutely necessary
  // You can use up to 16 timer for each ISR_Timer
  ISR_Timer.setInterval(TIMER_INTERVAL_50ms, timer_handler);

  // ============== MPU6050 ==============
  cali_sum_x = 0.0;
  cali_sum_y = 0.0;
  cali_sum_z = 0.0;

  // Try to initialize!
  mpu.begin();

  mpu.setAccelerometerRange(MPU6050_RANGE_2_G);
  mpu.setGyroRange(MPU6050_RANGE_250_DEG);
  mpu.setFilterBandwidth(MPU6050_BAND_10_HZ);
  delay(10);

  gyroZangle = 0.0;

  yy = 0;
  dev_yy = 0;

  timer = micros();
}

void startAdv(void)
{
  // Advertising packet
  Bluefruit.Advertising.addFlags(BLE_GAP_ADV_FLAGS_LE_ONLY_GENERAL_DISC_MODE);
  Bluefruit.Advertising.addTxPower();

  // Include bleuart 128-bit uuid
  Bluefruit.Advertising.addService(bleuart);

  // Secondary Scan Response packet (optional)
  // Since there is no room for 'Name' in Advertising packet
  Bluefruit.ScanResponse.addName();

  /* Start Advertising
   * - Enable auto advertising if disconnected
   * - Interval:  fast mode = 20 ms, slow mode = 152.5 ms
   * - Timeout for fast mode is 30 seconds
   * - Start(timeout) with timeout = 0 will advertise forever (until connected)
   * 
   * For recommended advertising interval
   * https://developer.apple.com/library/content/qa/qa1931/_index.html   
   */
  Bluefruit.Advertising.restartOnDisconnect(true);
  Bluefruit.Advertising.setInterval(32, 244);    // in unit of 0.625 ms
  Bluefruit.Advertising.setFastTimeout(30);      // number of seconds in fast mode
  Bluefruit.Advertising.start(0);                // 0 = Don't stop advertising after n seconds  
}

void loop()
{
  // Forward from BLEUART to HW Serial
  if ( bleuart.available() )
  {
    // char ch[msg_bye_cnt+1] = {0};
    int ch = 0;
    ch = bleuart.read(recv_msg, msg_bye_cnt);

    recv_cmd = recv_msg[3];

    bleuart.flush();

    if (recv_msg[2] == node_address) // Cmd is for this ant.
    {
      if (recv_msg[3] == 0xAA) { // Start cmd
        start_cmd_flag = 1;
        stop_cmd_flag  = 0;
        cali_cmd_flag  = 0;
        cali_done_flag = 0;
        // send back command ack
        bleuart.write(start_ack_buf, msg_bye_cnt);
        delay(5);
      }
      else if (recv_msg[3] == 0xEE) { // Stop cmd
        start_cmd_flag = 0;
        stop_cmd_flag  = 1;
        cali_cmd_flag  = 0;
        cali_done_flag = 0;

        yy_acc = 0;
        yy_pre = 0;
        yy = 0;
        dev_yy = 0;

        gyroZangle = 0.0;

        // send back command ack
        bleuart.write(stop_ack_buf, msg_bye_cnt);
        delay(5);
      }
      else if (recv_msg[3] == 0x11) { // Cali cmd
        start_cmd_flag = 0;
        stop_cmd_flag  = 0;
        cali_cmd_flag  = 1;
        cali_done_flag = 0;
        // send back command ack
        delay(5);
      }
      else { // Wrong cmd
        start_cmd_flag = 0;
        stop_cmd_flag  = 0;
        cali_cmd_flag  = 0;
        cali_done_flag = 0;
        // send back command ack
        bleuart.write(err_ack_buf, msg_bye_cnt);
        delay(5);
      }
    }
  }

  if (timer4Interrupt == true)
  {
    // ============= capturing gyro data in shift register =============
    sensors_event_t a, g, temp;
    mpu.getEvent(&a, &g, &temp);

    gyroXrate = (g.gyro.x)*57.2958-cali_x;
    gyroYrate = (g.gyro.y)*57.2958-cali_y;
    gyroZrate = (g.gyro.z)*57.2958-cali_z;

    // Storing data in shift registers
    for (ix=cali_data_len-1; ix>0; ix--)
      shift_reg_x[ix] = shift_reg_x[ix-1];
    shift_reg_x[0] = gyroXrate;

    for (iy=cali_data_len-1; iy>0; iy--)
      shift_reg_y[iy] = shift_reg_y[iy-1];
    shift_reg_y[0] = gyroYrate;

    for (iz=cali_data_len-1; iz>0; iz--)
      shift_reg_z[iz] = shift_reg_z[iz-1];
    shift_reg_z[0] = gyroZrate;

    // ====================================================
    // ===               Cali command                   ===
    // ====================================================
    // Got the cali cmd and the cali is not done
    if (cali_cmd_flag == 1 && cali_done_flag == 0)
    {
      cali_sum_x = 0.0;
      cali_sum_y = 0.0;
      cali_sum_z = 0.0;

      for (ix=0; ix<cali_data_len; ix++) cali_sum_x += shift_reg_x[ix];
      for (iy=0; iy<cali_data_len; iy++) cali_sum_y += shift_reg_y[iy];
      for (iz=0; iz<cali_data_len; iz++) cali_sum_z += shift_reg_z[iz];

      cali_bias_x = cali_sum_x/cali_data_len;
      cali_bias_y = cali_sum_y/cali_data_len;
      cali_bias_z = cali_sum_z/cali_data_len;

      // calculate bias
      cali_x = cali_bias_x + cali_x;
      cali_y = cali_bias_y + cali_y;
      cali_z = cali_bias_z + cali_z;

      cali_done_flag = 1;

      bleuart.write(cali_ack_buf, msg_bye_cnt);
    }

    if (start_cmd_flag == 1)
    {
      // =================== Run motor ===================
      run_motor();

      // =================== Frame number ===================
      reply_buf[3] = counter;

      // =================== Read Battery level ===================
      battValue = analogRead(batt_pin);
      batt_v = float(battValue)/1024*3.3*2*1.09*1000;

      if(batt_v<3300) batt_level = 0;
      if(batt_v<3600) batt_level = (batt_v-3300)/30;
      else {
        batt_v = batt_v-3600;
        batt_level = (10 + (batt_v * 0.15F ))>100? 100:(10 + (batt_v * 0.15F ));
      }
      reply_buf[10] = batt_level;

      // =================== Encoder ===================
      reply_buf[8] = encoder1Counter/256;
      reply_buf[9] = encoder2Counter/256;

      // =================== PID control ===================
      float dt = (float)(micros() - timer) / 1000000; // Calculate delta time
      timer = micros();

      gyroZangle += gyroZrate * dt;

      byte * bz = (byte *) &gyroZangle;

      memcpy(&reply_buf[4], bz, 4);

      dev_encoder2Counter = encoder2Counter - encoder2Counter_pre;
      if (dev_encoder2Counter < 0)  dev_encoder2Counter += 255;
      encoder2Counter_pre = encoder2Counter;

      dev_Zangle = gyroZangle - gyroZangle_pre;
      gyroZangle_pre = gyroZangle;

      yy_acc += yy;
      yy_pre = yy;
      yy = yy_pre + dev_encoder2Counter * sin(dev_Zangle * 0.0174533);
      dev_yy = yy - yy_pre;

      steer_f = (-tau_p * yy) - (tau_d * dev_yy) - (tau_i * yy_acc);
      steer = round(steer_f);

      if (steer >= (255-motor_speed)) steer = 255-motor_speed;
      else if (steer <= -motor_speed) steer = -motor_speed;

      byte * steer_b = (byte *) &steer;
      memcpy(&reply_buf[11], steer_b, 4);

      // =================== Send data back ===================
      bleuart.write(reply_buf, msg_bye_cnt);

      digitalWrite(LED_RED, !digitalRead(LED_RED));
    }
    else if (stop_cmd_flag == 1)
    {
      analogWrite(M1_IN1, 0);
      analogWrite(M1_IN2, 0);

      analogWrite(M2_IN1, 0);
      analogWrite(M2_IN2, 0);

      encoder1Counter = 0;
      encoder2Counter = 0;
    }
    timer4Interrupt = false;
  }
}

void stop_motor() {
  analogWrite(M1_IN1, 0);
  analogWrite(M1_IN2, 0);

  analogWrite(M2_IN1, 0);
  analogWrite(M2_IN2, 0);
}

void run_motor() {
  // NO PID
  analogWrite(M1_IN1, motor_speed+30);
  analogWrite(M1_IN2, 0);

  analogWrite(M2_IN1, 0);
  analogWrite(M2_IN2, motor_speed);

  // for PID
  /*
  analogWrite(M1_IN1, motor_speed + steer);
  analogWrite(M1_IN2, 0);

  analogWrite(M2_IN1, 0);
  analogWrite(M2_IN2, motor_speed);
  */
}

void timer_handler() {
  timer4Interrupt = true;
  counter++;
}

//------------HANDLE ENCODER INTERRUPTS---------------
void ENC1_INT_Routine() { 
  encoder1Counter++; 
}

void ENC2_INT_Routine() { 
  encoder2Counter++;
}

// callback invoked when central connects
void connect_callback(uint16_t conn_handle)
{
  // Get the reference to current connection
  BLEConnection* connection = Bluefruit.Connection(conn_handle);

  char central_name[32] = { 0 };
  connection->getPeerName(central_name, sizeof(central_name));

  // Serial.print("Connected to ");
  // Serial.println(central_name);
}

// going forward for a distance (dist), in mm
void going_forward(int dist) {
  int enl_target = (dist-bb)/aa;
}

// Turning an angle (dist), in degree
void turning_angle(int angle) {
  ;
}

/**
 * Callback invoked when a connection is dropped
 * @param conn_handle connection where this event happens
 * @param reason is a BLE_HCI_STATUS_CODE which can be found in ble_hci.h
 */
void disconnect_callback(uint16_t conn_handle, uint8_t reason)
{
  (void) conn_handle;
  (void) reason;

  // Serial.println();
  // Serial.print("Disconnected, reason = 0x");
  // Serial.println(reason, HEX);
}

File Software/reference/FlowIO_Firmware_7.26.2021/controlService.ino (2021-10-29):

void createControlService(void) {
  uint8_t controlServiceUUID[16]   = {0x04,0xaa,0x00,0x00,0x00,0x00,0x0b,0x0b,0x0b,0x0b,0x0b,0x0b,0x0b,0x0b,0x0b,0x0b}; //"0b0b0b0b-0b0b-0b0b-0b0b-00000000aa04"
  uint8_t chrCommandUUID[16]       = {0x04,0xaa,0x00,0x00,0x00,0xc1,0x0b,0x0b,0x0b,0x0b,0x0b,0x0b,0x0b,0x0b,0x0b,0x0b}; //"0b0b0b0b-0b0b-0b0b-0b0b-c1000000aa04"
  uint8_t chrHardwareStateUUID[16]= {0x04,0xaa,0x00,0x00,0x00,0xc2,0x0b,0x0b,0x0b,0x0b,0x0b,0x0b,0x0b,0x0b,0x0b,0x0b}; //"0b0b0b0b-0b0b-0b0b-0b0b-c2000000aa04"

  controlService = BLEService(controlServiceUUID);
  controlService.begin();

  chrCommand = BLECharacteristic(chrCommandUUID);
  chrCommand.setProperties(CHR_PROPS_WRITE);
  chrCommand.setWriteCallback(onWrite_chrCommand);
  chrCommand.setPermission(SECMODE_OPEN, SECMODE_OPEN);
  chrCommand.setFixedLen(3);
  chrCommand.begin();

  chrHardwareState = BLECharacteristic(chrHardwareStateUUID);
  chrHardwareState.setProperties(CHR_PROPS_NOTIFY | CHR_PROPS_READ);
  chrHardwareState.setPermission(SECMODE_OPEN, SECMODE_OPEN);
  chrHardwareState.setFixedLen(2);
  chrHardwareState.begin();
  chrHardwareState.write16(flowio.getHardwareState());
}

//This is executed when a central device writes to the characteristic.
void onWrite_chrCommand(uint16_t conn_hdl, BLECharacteristic* chr, uint8_t* data, uint16_t len) {
  Serial.println("Value Written");  
  //data[0]=action, data[1]=port, data[2]=pwm
  if(len==2){
    Serial.print(data[0],BIN);
    Serial.println(data[1],BIN);
    flowio.command(data[0],data[1]);
  }
  else if(len==3){ //TODO: I need to know which byte is what.
    Serial.print(data[0],BIN);
    Serial.println(data[1],BIN);
    Serial.println(data[2],BIN);
    flowio.command(data[0],data[1],data[2]);
  }
  chrHardwareState.notify16(flowio.getHardwareState());
}

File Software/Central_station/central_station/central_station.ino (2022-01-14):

/* This sketch demonstrates the central API() that allows you to connect
 * to multiple peripherals boards (Bluefruit nRF52 in peripheral mode, or
 * any Bluefruit nRF51 boards).
 *
 * One or more Bluefruit boards, configured as a peripheral with the
 * bleuart service running are required for this demo.
 *
 * This sketch will: 
 *  - Read data from the HW serial port (normally USB serial, accessible
 *    via the Serial Monitor for example), and send any incoming data to
 *    all other peripherals connected to the central device.
 *  - Forward any incoming bleuart messages from a peripheral to all of
 *    the other connected devices.
 * 
 * It is recommended to give each peripheral board a distinct name in order
 * to more easily distinguish the individual devices.
 * 
 * Connection Handle Explanation
 * -----------------------------
 * The total number of connections is BLE_MAX_CONNECTION (20)
 * 
 * The 'connection handle' is an integer number assigned by the SoftDevice
 * (Nordic's proprietary BLE stack). Each connection will receive it's own
 * numeric 'handle' starting from 0 to BLE_MAX_CONNECTION-1, depending on the order
 * of connection(s).
 *
 * - E.g If our Central board connects to a mobile phone first (running as a peripheral),
 * then afterwards connects to another Bluefruit board running in peripheral mode, then
 * the connection handle of mobile phone is 0, and the handle for the Bluefruit
 * board is 1, and so on.
 */

#include <bluefruit.h>

// Struct containing peripheral info
typedef struct
{
  char name[16+1];

  uint16_t conn_handle;

  // Each prph need its own bleuart client service
  BLEClientUart bleuart;
} prph_info_t;

/* Peripheral info array (one per peripheral device)
 * 
 * There are 'BLE_MAX_CONNECTION' central connections, but the
 * the connection handle can be numerically larger (for example if
 * the peripheral role is also used, such as connecting to a mobile
 * device). As such, we need to convert connection handles <-> the array
 * index where appropriate to prevent out of array accesses.
 * 
 * Note: One can simply declares the array with BLE_MAX_CONNECTION and use connection
 * handle as index directly with the expense of SRAM.
 */
prph_info_t prphs[BLE_MAX_CONNECTION];

// Software Timer for blinking the RED LED
SoftwareTimer blinkTimer;
uint8_t connection_num = 0; // for blink pattern

// How many bytes in a msg
#define data_cnt 20

// uint8_t tst_cmd[data_cnt+1] = {0xEB,0x90,0x00,0xAA,0x00,0x00,0x00,0x00,0x00,0x00,0x00,0x00,0x00,0x00,0x00,0x00,0x00,0x00,0x00,0x25};

uint8_t start_cmd[data_cnt+1] = {0xEB,0x90,0x00,0xAA,0x00,0x00,0x00,0x00,0x00,0x00,0x00,0x00,0x00,0x00,0x00,0x00,0x00,0x00,0x00,0xAF};
uint8_t stop_cmd[data_cnt+1]  = {0xEB,0x90,0x00,0xEE,0x00,0x00,0x00,0x00,0x00,0x00,0x00,0x00,0x00,0x00,0x00,0x00,0x00,0x00,0x00,0xAF};
uint8_t cali_cmd[data_cnt+1]  = {0xEB,0x90,0x00,0x11,0x00,0x00,0x00,0x00,0x00,0x00,0x00,0x00,0x00,0x00,0x00,0x00,0x00,0x00,0x00,0xAF};

uint8_t which_ant[data_cnt+1] = {0xEB,0xFF,0x00,0x00,0x00,0x00,0x00,0x00,0x00,0x00,0x00,0x00,0x00,0x00,0x00,0x00,0x00,0x00,0x00,0x00};
uint8_t ant_stop[data_cnt+1]  = {0xEB,0x11,0x00,0x00,0x00,0x00,0x00,0x00,0x00,0x00,0x00,0x00,0x00,0x00,0x00,0x00,0x00,0x00,0x00,0x00};

// command back to PC t indicate a new robot connection
uint8_t connection_ack[data_cnt+1]  = {0xEB,0xAA,0x00,0x00,0x00,0x00,0x00,0x00,0x00,0x00,0x00,0x00,0x00,0x00,0x00,0x00,0x00,0x00,0x00,0x00};

int CMD_TST_PIN = 9;
int CMD_TST_PIN_val = 0;
int CMD_TST_sent_flag = 0;

// ============= Control pins for each robot =============
// #4: bridging test
int CALI_CMD_PIN_4  = 22; // b1
int START_CMD_PIN_4 = 5;  // b2
int STOP_CMD_PIN_4  = 6;  // b3

// #5: impedance test
int CALI_CMD_PIN_5  = 11; // b4
int START_CMD_PIN_5 = 10; // b5
int STOP_CMD_PIN_5  = 9;  // b6

// #1: knocking
int START_CMD_PIN_1 = 13; // b7
int STOP_CMD_PIN_1  = 12; // b8

// #2: tracking
int CALI_CMD_PIN_2  = A5; // b9
int START_CMD_PIN_2 = A4; // b10
int STOP_CMD_PIN_2  = A3; // b11

// #0: Temperature
int CALI_CMD_PIN_0  = A0; // b12
int START_CMD_PIN_0 = A1; // b13
int STOP_CMD_PIN_0  = A2; // b14

int CALI_CMD_PIN_val  = 0;
int START_CMD_PIN_val = 0;
int STOP_CMD_PIN_val  = 0;

int CALI_CMD_sent_flag  = 0;
int START_CMD_sent_flag = 0;
int STOP_CMD_sent_flag  = 0;

void setup() 
{
  Serial.begin(115200);
  while ( !Serial ) delay(10);   // for nrf52840 with native usb

  // Initialize blinkTimer for 100 ms and start it
  blinkTimer.begin(100, blink_timer_callback);
  blinkTimer.start();

  pinMode(CALI_CMD_PIN_4, INPUT);
  pinMode(START_CMD_PIN_4, INPUT);
  pinMode(STOP_CMD_PIN_4, INPUT);

  pinMode(CALI_CMD_PIN_5, INPUT);
  pinMode(START_CMD_PIN_5, INPUT);
  pinMode(STOP_CMD_PIN_5, INPUT);

  pinMode(START_CMD_PIN_1, INPUT);
  pinMode(STOP_CMD_PIN_1, INPUT);

  pinMode(CALI_CMD_PIN_2, INPUT);
  pinMode(START_CMD_PIN_2, INPUT);
  pinMode(STOP_CMD_PIN_2, INPUT);

  pinMode(CALI_CMD_PIN_0, INPUT);
  pinMode(START_CMD_PIN_0, INPUT);
  pinMode(STOP_CMD_PIN_0, INPUT);

  // attachInterrupt(digitalPinToInterrupt(CMD_TST_PIN), send_tst_cmd, FALLING);

  // Serial.println("Bluefruit52 Central Multi BLEUART Example");
  // Serial.println("-----------------------------------------\n");

  // Initialize Bluefruit with max concurrent connections as Peripheral = 0, Central = 4
  // SRAM usage required by SoftDevice will increase with number of connections
  Bluefruit.begin(0, 4);

  // Set Name
  Bluefruit.setName("Bluefruit52 Central");

  // Init peripheral pool
  for (uint8_t idx=0; idx<BLE_MAX_CONNECTION; idx++)
  {
    // Invalid all connection handle
    prphs[idx].conn_handle = BLE_CONN_HANDLE_INVALID;

    // All of BLE Central Uart Serivce
    prphs[idx].bleuart.begin();
    prphs[idx].bleuart.setRxCallback(bleuart_rx_callback);
  }

  // Callbacks for Central
  Bluefruit.Central.setConnectCallback(connect_callback);
  Bluefruit.Central.setDisconnectCallback(disconnect_callback);

  /* Start Central Scanning
   * - Enable auto scan if disconnected
   * - Interval = 100 ms, window = 80 ms
   * - Filter only accept bleuart service in advertising
   * - Don't use active scan (used to retrieve the optional scan response adv packet)
   * - Start(0) = will scan forever since no timeout is given
   */
  Bluefruit.Scanner.setRxCallback(scan_callback);
  Bluefruit.Scanner.restartOnDisconnect(true);
  Bluefruit.Scanner.setInterval(160, 80);       // in units of 0.625 ms
  Bluefruit.Scanner.filterUuid(BLEUART_UUID_SERVICE);
  Bluefruit.Scanner.useActiveScan(false);       // Don't request scan response data
  Bluefruit.Scanner.start(0);                   // 0 = Don't stop scanning after n seconds
}
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

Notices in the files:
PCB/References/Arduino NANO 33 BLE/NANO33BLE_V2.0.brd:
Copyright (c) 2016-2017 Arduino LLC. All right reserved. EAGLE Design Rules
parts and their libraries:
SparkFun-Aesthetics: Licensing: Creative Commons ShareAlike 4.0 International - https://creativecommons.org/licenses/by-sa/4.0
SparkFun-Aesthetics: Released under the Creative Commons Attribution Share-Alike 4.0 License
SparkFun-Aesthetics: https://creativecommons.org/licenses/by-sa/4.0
